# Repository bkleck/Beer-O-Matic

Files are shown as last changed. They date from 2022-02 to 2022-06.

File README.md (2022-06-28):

# Beer-O-Matic
Automatic Beer Dispenser



## Table of Contents
* [Introduction](#introduction)
* [Mechanical Design](#mechanical-design)
* [Code Documentation](#code-documentation)
* [Logic Diagram](#logic-diagram)
* [Wiring Diagram](#wiring-diagram)

## Introduction
This project was done as part of the **_ME102B Mechatronics Design_** course during my exchange in UC Berkeley. We had to produce a working prototype by the end of the semester, that solves a problem in real life. We had to do both **_mechanical design and code design_** for our prototype to work.

We decided to do something fun, and decided to build a **_automatic beer dispenser_**. This solves the problem which one might experience in a crowded bar, trying to get the attention of the bartender but to no avail. With our product, you will be able to get a cold pint of beer without the need to ask anybody!

## Mechanical Design


- A **_rack and pinion_** was designed so that the motor can move the dispensing spout along the rack to get to its **_target destination_**.
- A **_cup holder_** is placed at every seat so that the user can put their glass into the holder when they require a drink. A small **_push against the in-built button_** will signal to the system that the user **_requires a refill_**, without the need for manual effort.
- The 2 main sensors we used were the **_limit switches and the IR sensors_**. The limit switches will be placed on each end to signal to our system that it has reached the corners and to change direction, **_preventing our spout from falling off_** the rack. The IR sensors will be placed at each of the cup holders. This will help to track the moving spout, as well as to tell the system to **_stop when it has reached the target holder_**.

## Code Documentation
### 1) Position tracking
On `Startup()`, we will turn the motor anticlockwise to move left, and stop when it has reached the left limit. Afterwards, the direction will be reversed and `currentPos` will be set to 0, representing the left limit switch. There will be **_3 IR sensors_** in our demo, so each of them will be labelled 1,2,3 respectively and the right limit switch will be 4.

The `ReadTarget()` function will be used to **_add a target position_** to the queue. We will be using a **_FIFO queue system_** so that users can signal to the system that they require a drink at any point in time, without needing to wait for their turn. Whenever a user **_presses the button_** on the cup holder, the system will **_read the pin as LOW_** because we are using **_PULLUP mode_**. We will then **_check if the position is already in queue_** using the boolean variable `elementInside`. This prevents any user from hogging the system and prevent spillage in the event the user accidentally presses more than once. If `elementInside = false`, we will **_add that element into our_** `targetQueue` **_array_** at the next possible location.

The `ReadIRSensor()` function is used to **_determine if the moving spout passes by any of the IR sensors_**. It uses `analogRead` to determine the **_amount of light the IR sensor is receiving_** at that point in time. We will use the initial IR reading during startup to determine that as no object passing by. If the **_current reading drops 100 points below initial reading_**, this means the moving spout **_moved past_** and it will return a **_LOW value_**.

Our `MoveToTarget()` function does exactly what is said. The `targetPos` variable is the next position the spout needs to move to, which is the **_first element_** of the `targetQueue` array. Next, we will make use of the **_current position's index and target position's index to tell the spout where to move_**. If `targetIndex > currentIndex`, the spout needs to move right to reach the target, and vice versa. Once `targetPos == currentPos`, we have reached our destination and will **_dispense beer_** using `measure_dispense()` function. The element will also be **_removed from the queue_**. Another safety feature we had was that if the spout ever **_hits the left or right limit switches_**, we will **_reverse the direction_** so that it can continue to find the target position. This happens sometimes due to bugs in the IR sensors.

### 2) Dispensing
Firstly, to **_calculate the distance between the cup and pump_**, we have an **_ultrasound sensor_** attached to the spout. In the `calc_distance()` function, we will turn the trigger pin of this sensor from LOW to HIGH to LOW, and calculate the **_duration for the ultrasound wave to emit and reflect back_** from the bottom of the cup. The distance is then calculated by deriving from the **_duration recorded and the speed of sound in air_**.

Next, we will use the `measure_dispense()` function to actually dispense the beer in the given time. Firstly, we model our cup using a standard size of **_500ml_**, and we want the cup to be completely filled in **_~3s_**. Hence, we calculate the **_flow rate using volume/time_**. Afterwards, we calculate the rate of height increase required using **_height_rate = flow rate/surface area_**. Lastly, the **_time required for the dispense will be (distance - final_distance)/height_rate_**. We will then activate the relay pin to turn on the valve for the given amount of time. Another safety feature here is that when the valve is open, the motor will be turned off, and vice versa, to **_prevent any spillage_** from movement during dispensing.

## Logic Diagram
<p align="center">
  
  
  
</p>

## Wiring Diagram
<p align="center">
  
</p>

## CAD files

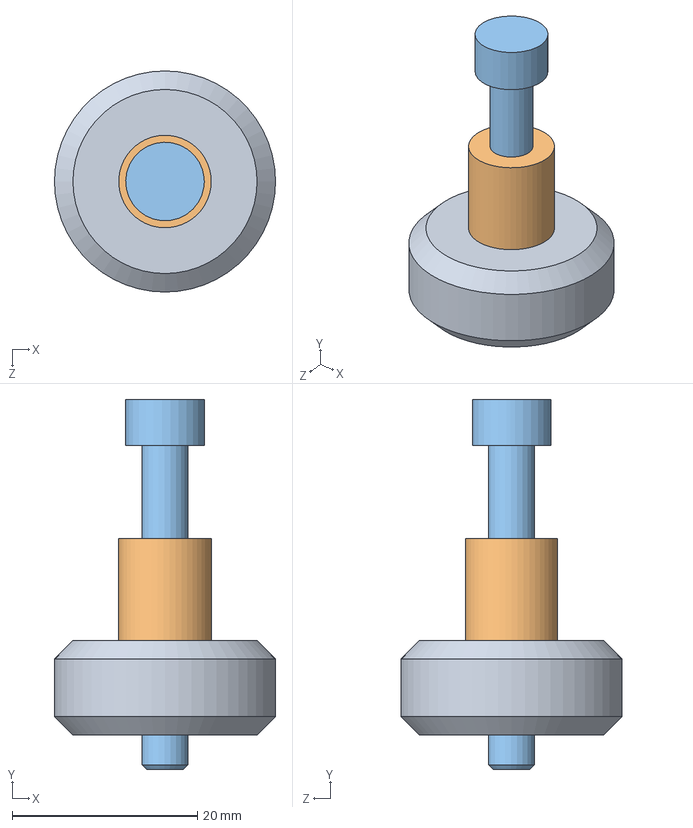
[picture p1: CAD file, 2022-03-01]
CAD files/PissBotV1 17-02-2022/PissBotV1 17-02/VWheelAssy.SLDASM
23.9 x 40.0 x 23.9 mm
Solid V Wheel
M5x9 Spacer
M5x40

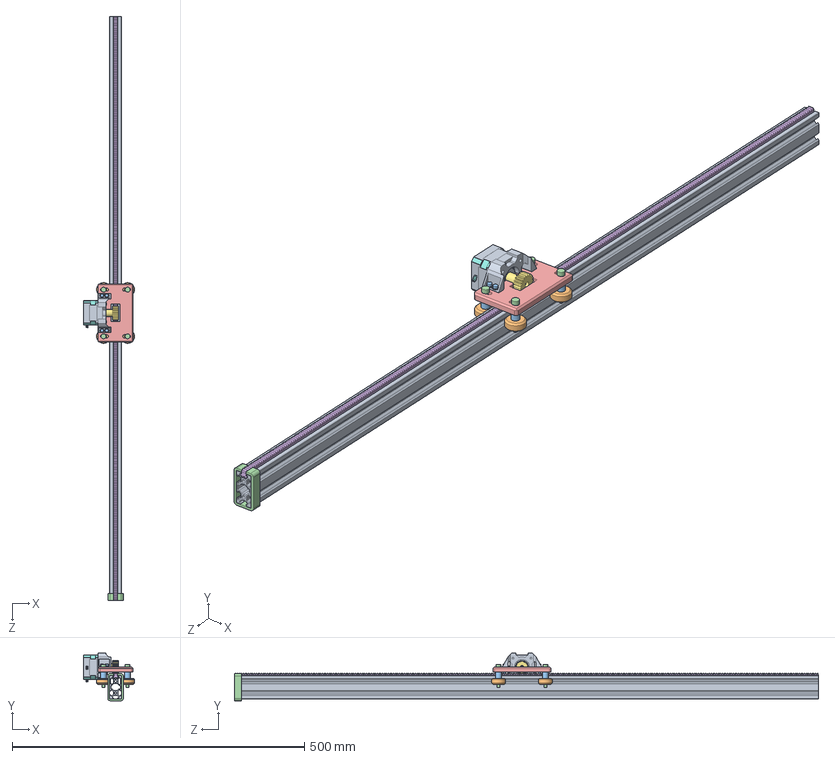
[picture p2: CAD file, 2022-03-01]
CAD files/All_Files_V1/PissBotV1.SLDASM
87.6 x 81.4 x 1000.0 mm
2040 V-Slot 500mm
Solid V Wheel x 4
M5x9 Spacer x 4
M5x40 x 4
Plate
Combined Rack Gear
Pinion Gear
Stepper Holder
M3 Washer x 8
M3x15 x 4
Rail Holder

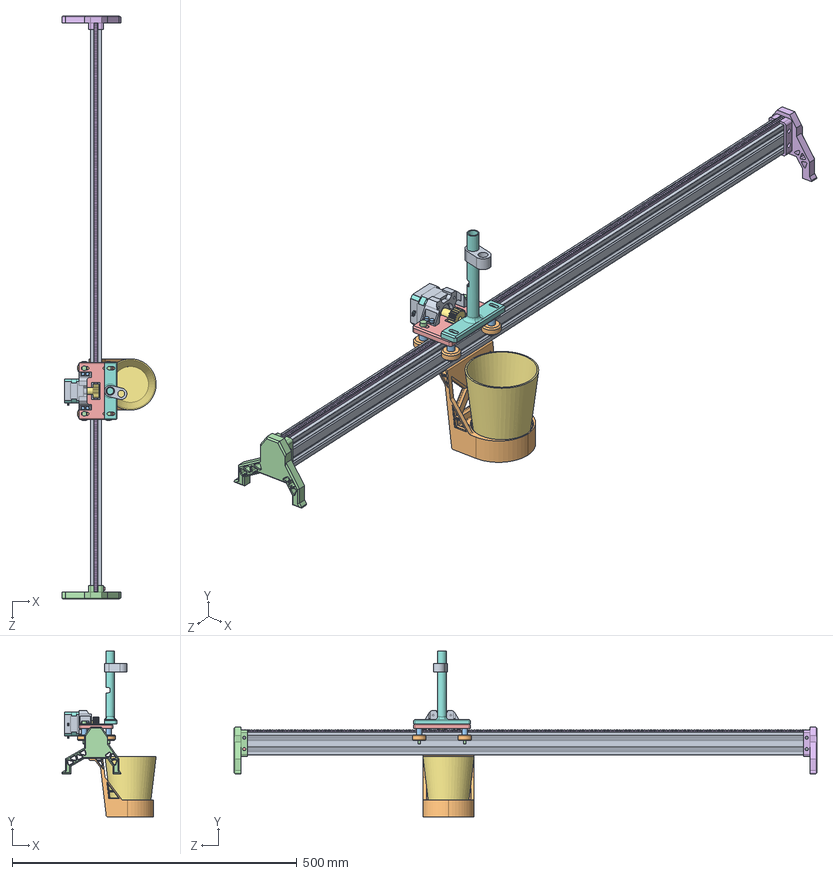
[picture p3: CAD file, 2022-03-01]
CAD files/PissBotV1 17-02-2022/PissBotV1 17-02/PissBotV1.SLDASM
165.7 x 291.1 x 1024.0 mm
2040 V-Slot 500mm
Solid V Wheel x 4
M5x9 Spacer x 4
M5x40 x 4
Plate
Combined Rack Gear
Pinion Gear
Stepper Holder
M3 Washer x 8
M3x15 x 4
Rail Holder
M4x8
Rail Holder Mirror
Cup
sprout_attachment
sprout_tip
Coaster V2

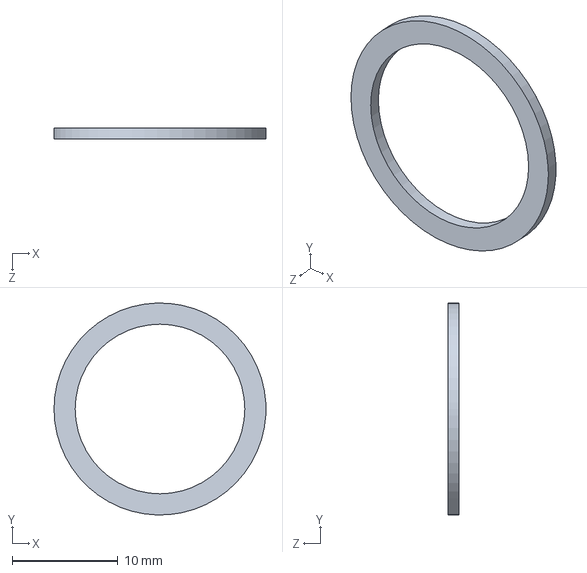
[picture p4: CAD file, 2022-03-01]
CAD files/All_Files_V1/Coaster Spacers.SLDPRT
20.0 x 20.0 x 1.00 mm

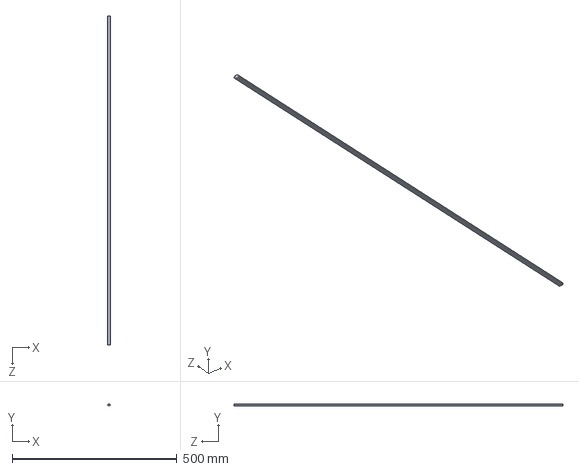
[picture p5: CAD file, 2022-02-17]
CAD files/Rack.SLDPRT
10.5 x 6.95 x 1000.0 mm

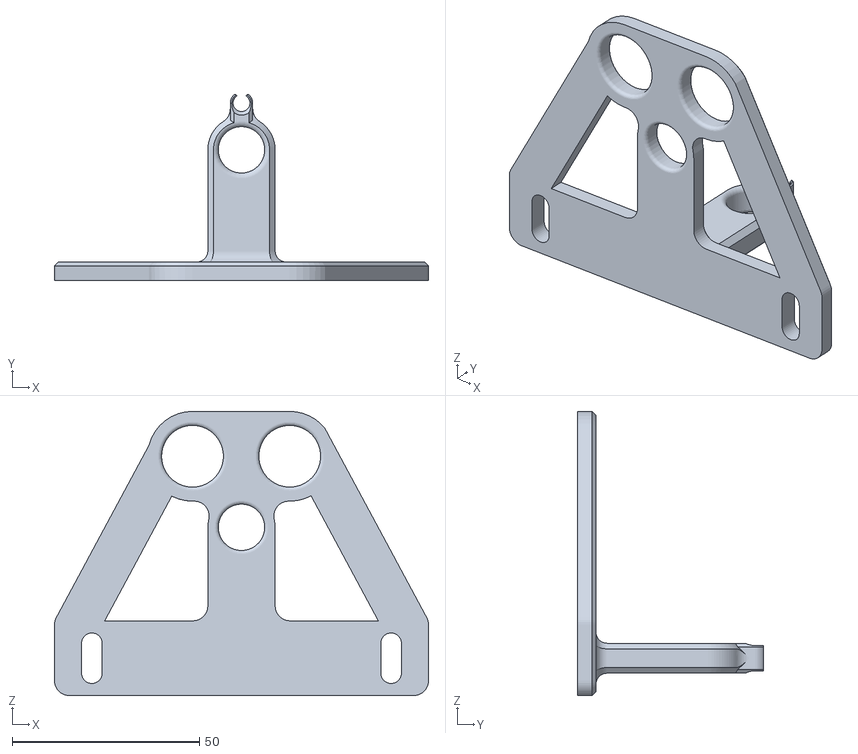
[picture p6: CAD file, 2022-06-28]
final CAD files/Spout V3.STL
100.0 x 49.9 x 76.0

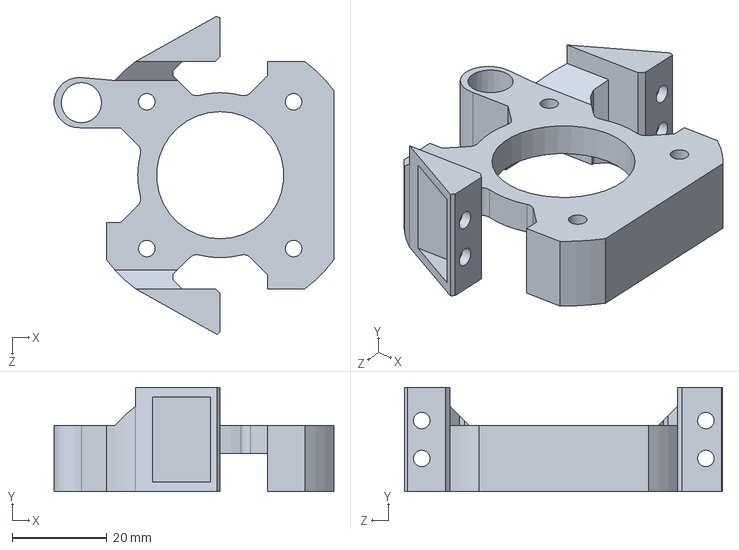
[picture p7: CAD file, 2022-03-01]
CAD files/All_Files_V1/Stepper Holder.sldprt
59.1 x 22.0 x 67.2 mm

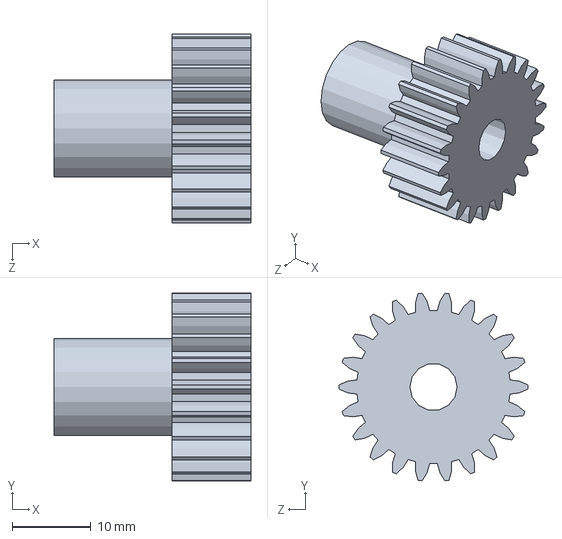
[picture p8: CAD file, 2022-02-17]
CAD files/Pinion Gear.SLDPRT
25.0 x 23.8 x 24.0 mm

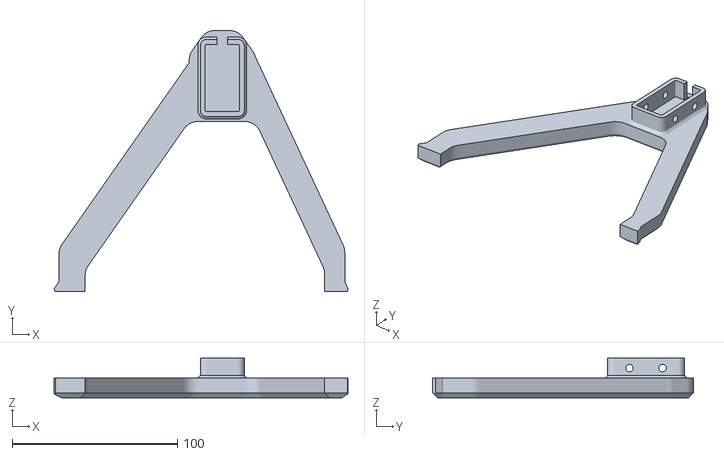
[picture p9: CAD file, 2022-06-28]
final CAD files/Rail Holder Mirror.STL
177.7 x 157.8 x 24.0

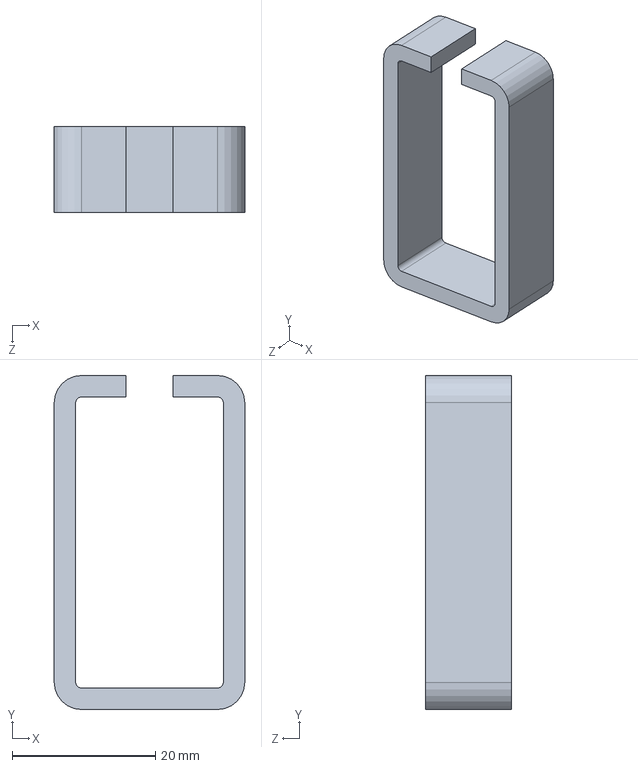
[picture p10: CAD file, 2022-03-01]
CAD files/All_Files_V1/Rail Holder.SLDPRT
26.6 x 46.6 x 12.0 mm

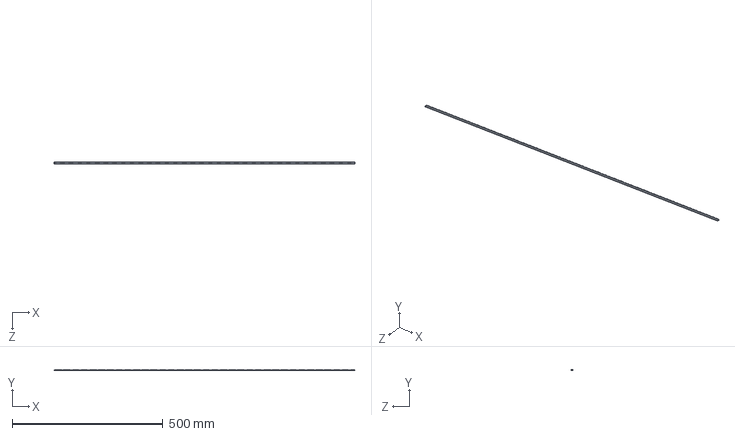
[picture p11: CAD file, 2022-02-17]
CAD files/Rack Gear.SLDPRT
1000.0 x 3.25 x 6.10 mm

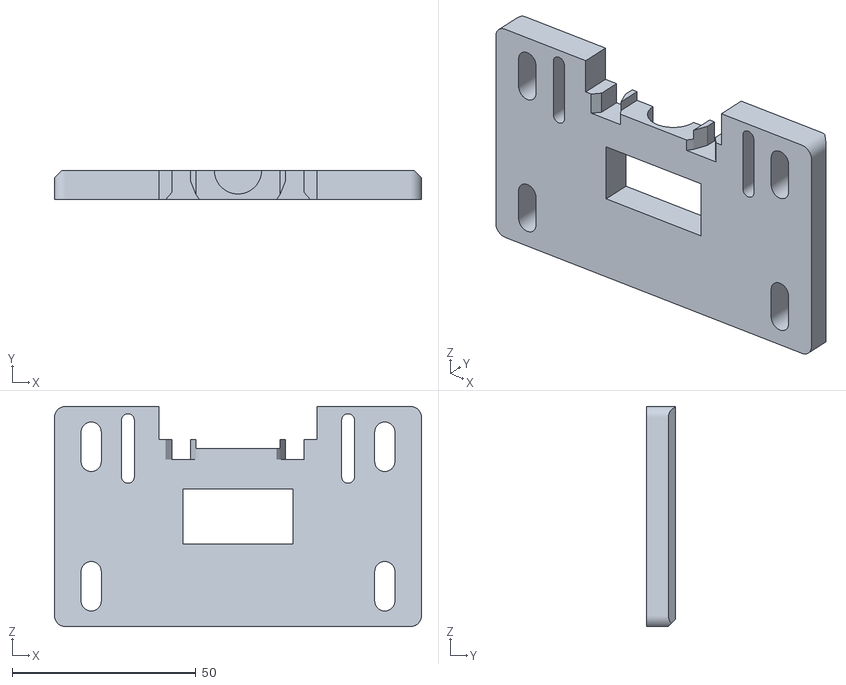
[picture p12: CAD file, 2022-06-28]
final CAD files/Plate.STL
100.0 x 8.00 x 60.0

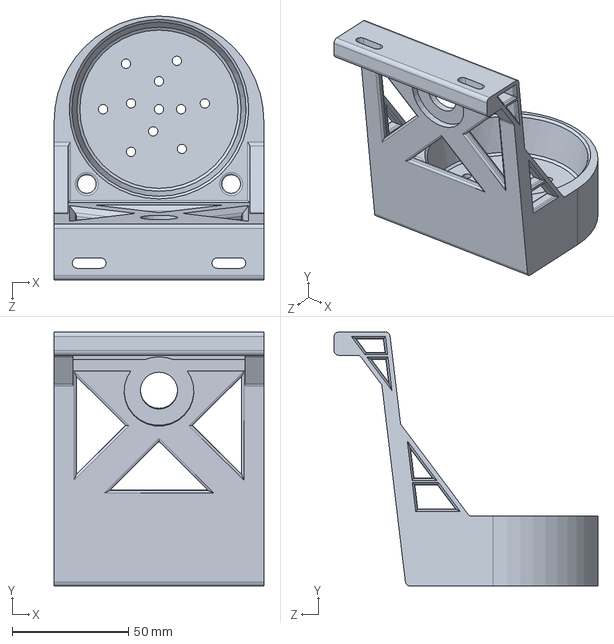
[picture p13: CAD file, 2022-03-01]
CAD files/All_Files_V1/Coaster V2.SLDPRT
90.0 x 109.0 x 113.3 mm

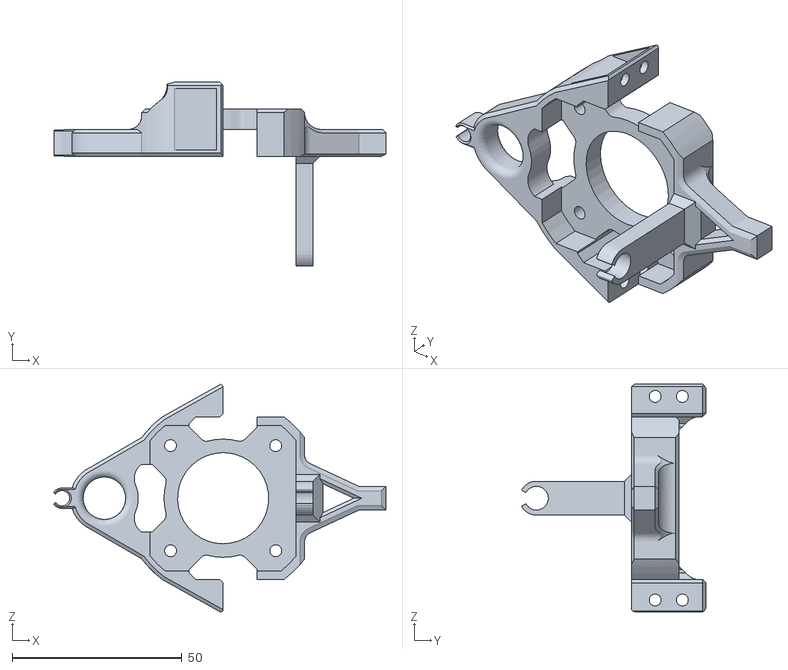
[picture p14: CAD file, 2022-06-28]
final CAD files/Stepper Holder.STL
97.9 x 54.3 x 67.2

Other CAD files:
CAD files/PissBotV1 17-02-2022/PissBotV1 17-02/VWheelAssy2.SLDASM
CAD files/PissBotV1 17-02-2022/PissBotV1 17-02/VWheelAssy4.SLDASM
CAD files/PissBotV1 17-02-2022/PissBotV1 17-02/VWheelAssy3.SLDASM
CAD files/All_Files_V1/Coaster.SLDPRT
CAD files/All_Files_V1/Cup.SLDPRT
CAD files/PissBotV1 17-02-2022/PissBotV1 17-02/2040 V-Slot 500mm.SLDPRT
CAD files/PissBotV1 17-02-2022/PissBotV1 17-02/9238.sldprt
CAD files/PissBotV1 17-02-2022/PissBotV1 17-02/Coaster.SLDPRT
CAD files/PissBotV1 17-02-2022/PissBotV1 17-02/Combined Rack Gear.SLDPRT
CAD files/PissBotV1 17-02-2022/PissBotV1 17-02/M3 Washer.SLDPRT
CAD files/PissBotV1 17-02-2022/PissBotV1 17-02/M3x15.SLDPRT
CAD files/PissBotV1 17-02-2022/PissBotV1 17-02/M4x8.SLDPRT
CAD files/PissBotV1 17-02-2022/PissBotV1 17-02/M5x40.SLDPRT
CAD files/PissBotV1 17-02-2022/PissBotV1 17-02/M5x9 Spacer.SLDPRT
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

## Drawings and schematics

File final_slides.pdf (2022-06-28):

# BEER - 0 -

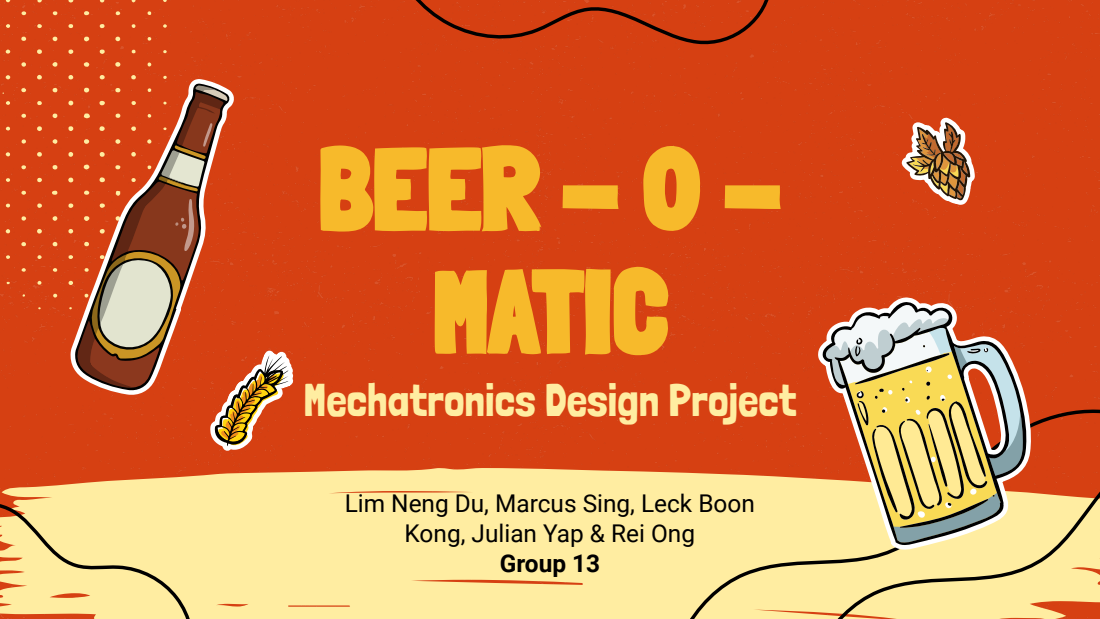
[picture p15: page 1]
MATIC; Group 13

Mechatronics Design Project

Lim Neng Du, Marcus Sing, Leck Boon
Kong, Julian Yap & Rei Ong

# Problem

# Solution

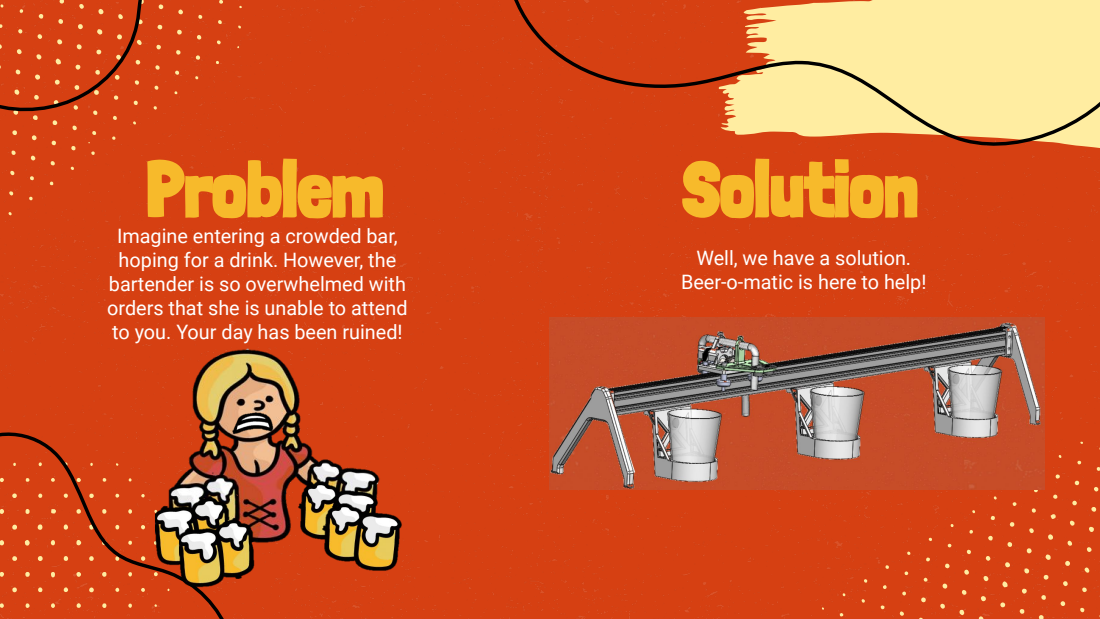
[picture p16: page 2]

Imagine entering a crowded bar,
hoping for a drink. However, the
bartender is so overwhelmed with
orders that she is unable to attend
to you. Your day has been ruined!

Well, we have a solution.
Beer-o-matic is here to help!

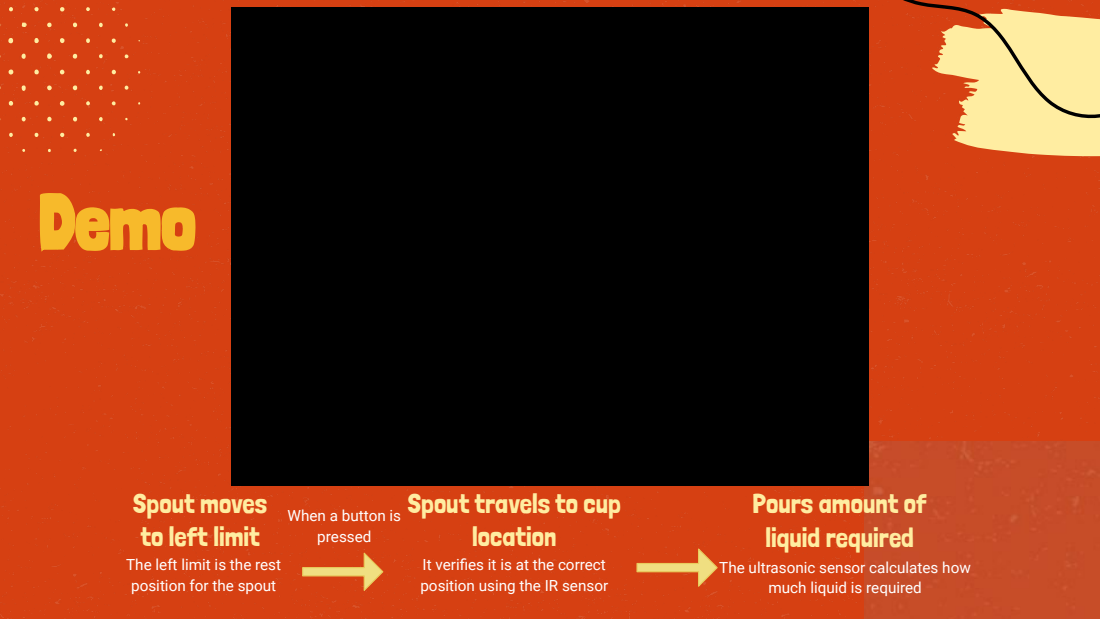
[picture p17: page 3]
Demo

Spout moves
to left limit

Spout travels to cup
location

Pours amount of
liquid required

When a button is
pressed

The left limit is the rest
position for the spout

It verifies it is at the correct
position using the IR sensor

The ultrasonic sensor calculates how

much liquid is required

# Logic Diagram

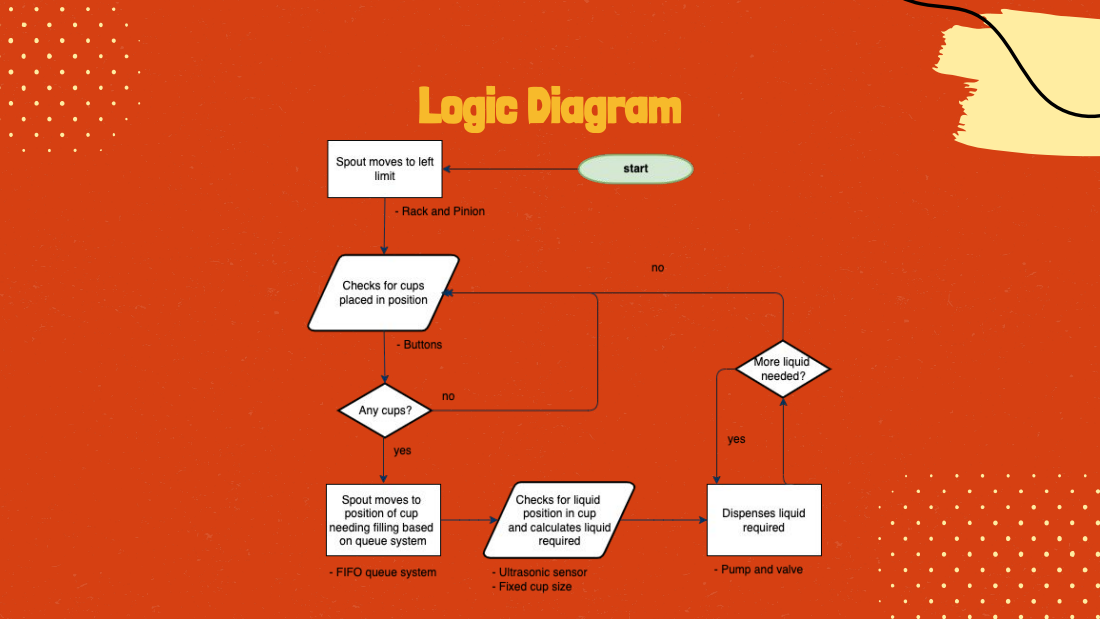
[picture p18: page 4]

# Logic Diagram

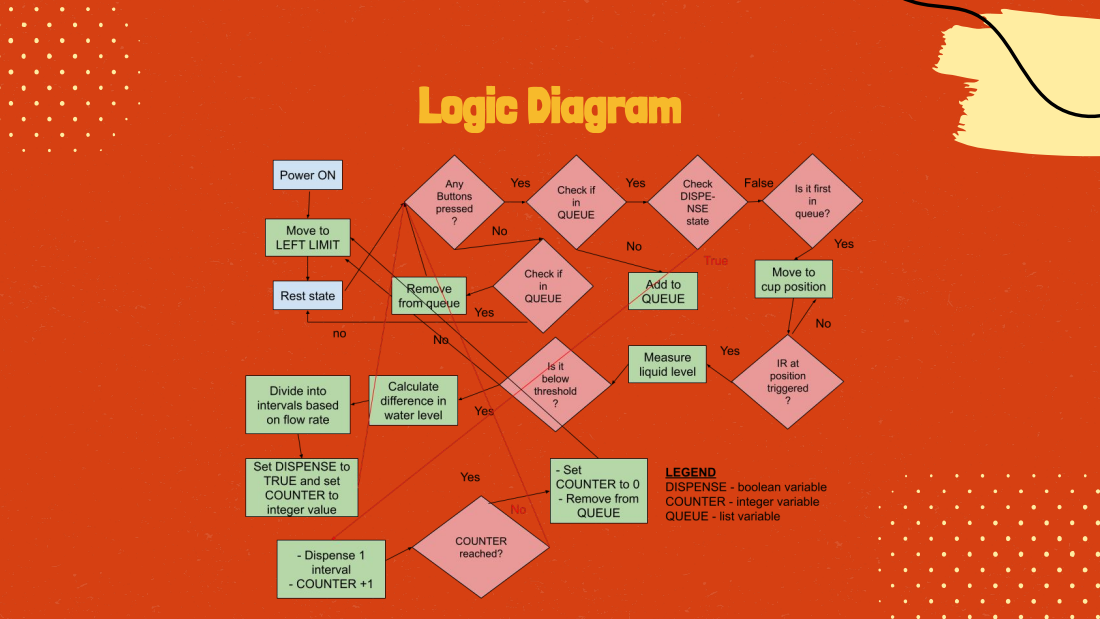
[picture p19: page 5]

# Physical characteristics

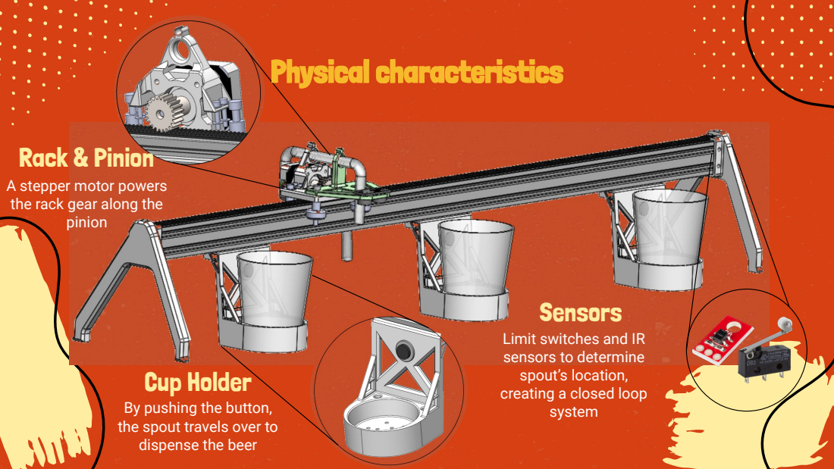
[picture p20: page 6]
Cup Holder; pinion; Sensors; system; Rack & Pinion

A stepper motor powers
the rack gear along the

Limit switches and IR
sensors to determine
spout’s location,
creating a closed loop

By pushing the button,
the spout travels over to
dispense the beer

# Program logic

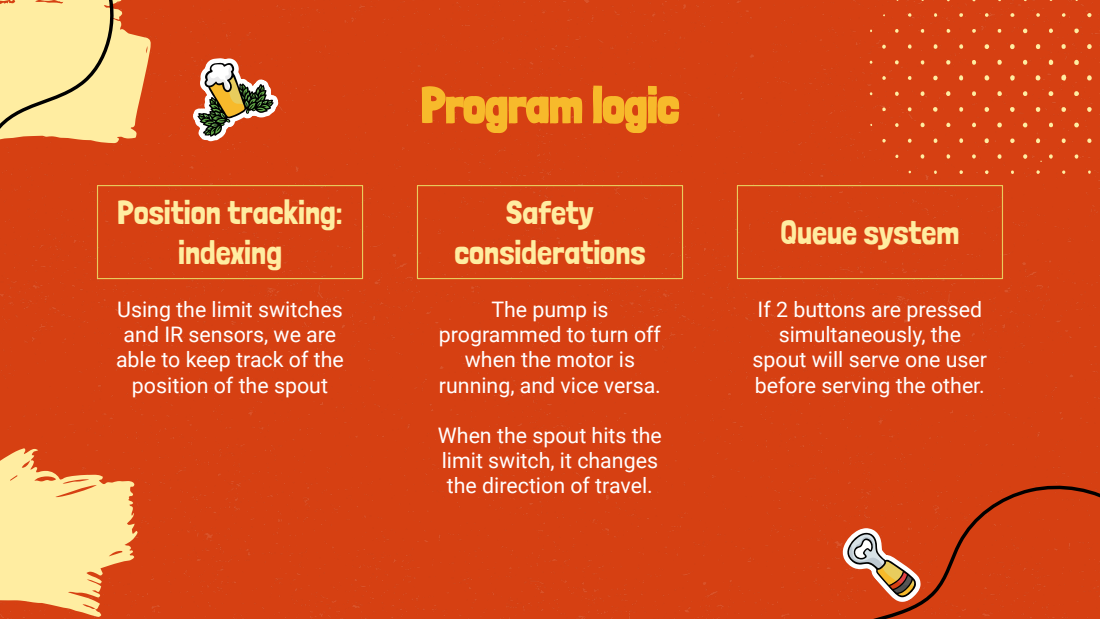
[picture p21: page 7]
Position tracking: indexing; Safety considerations; Queue system

Using the limit switches
and IR sensors, we are
able to keep track of the
position of the spout

The pump is
programmed to turn off
when the motor is
running, and vice versa.

If 2 buttons are pressed
simultaneously, the
spout will serve one user
before serving the other.

When the spout hits the
limit switch, it changes
the direction of travel.

# Engineering principles

# Pump System

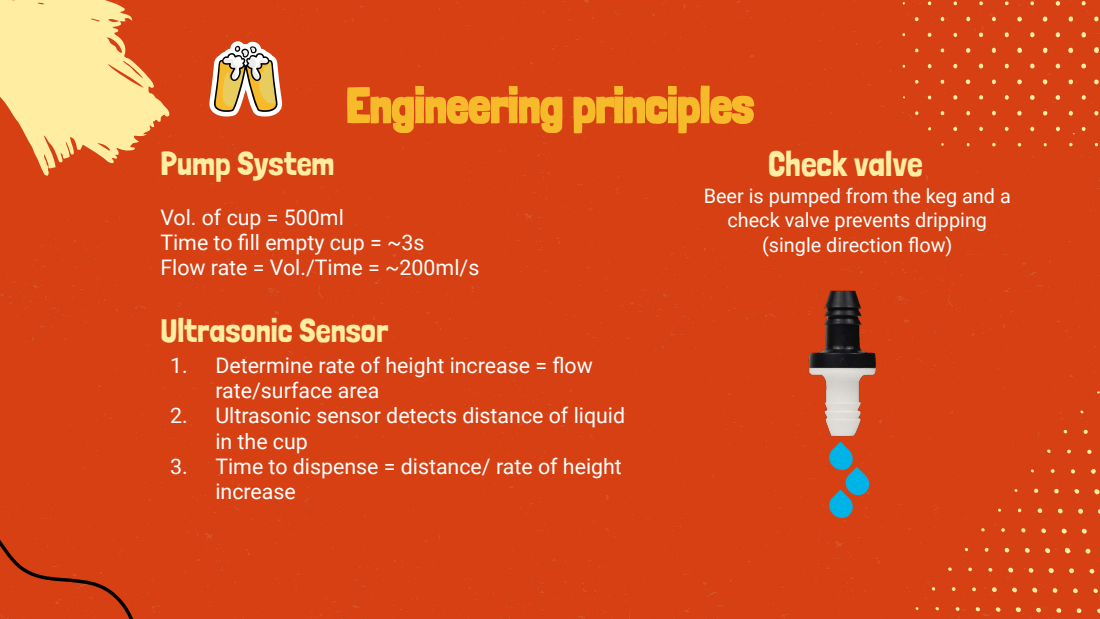
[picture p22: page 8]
Check valve

Beer is pumped from the keg and a
check valve prevents dripping
(single direction flow)

Vol. of cup = 500ml
Time to fill empty cup = ~3s
Flow rate = Vol./Time = ~200ml/s
Ultrasonic Sensor

1. Determine rate of height increase = flow
rate/surface area
2. Ultrasonic sensor detects distance of liquid
in the cup
3. Time to dispense = distance/ rate of height
increase

# Fluid Pump

# Linear Movement Spout

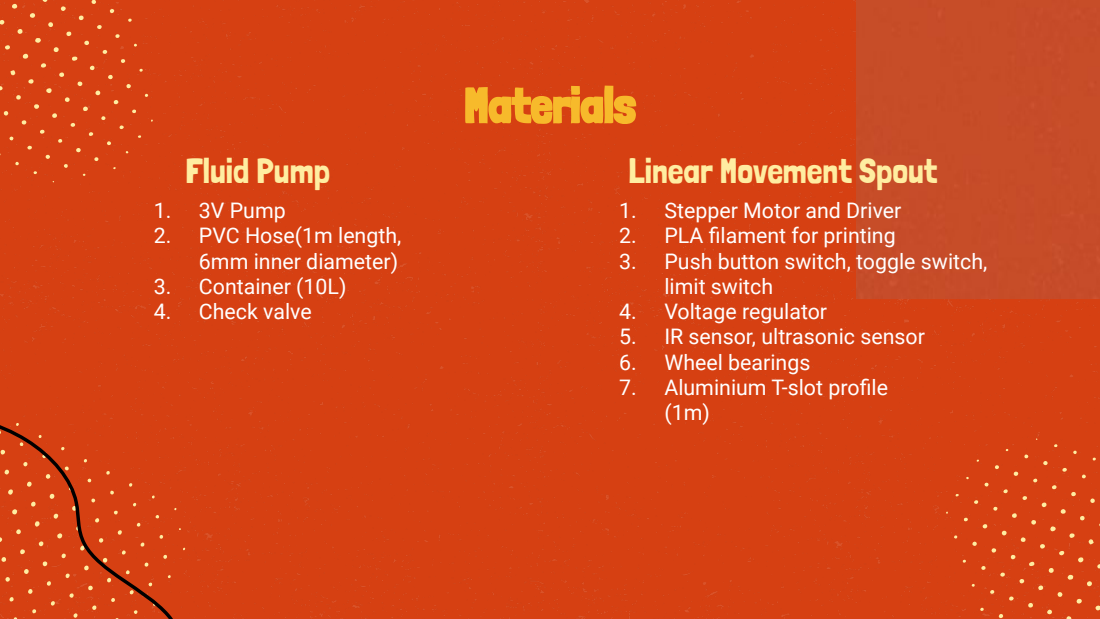
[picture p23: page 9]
Materials

1. 3V Pump
2. PVC Hose(1m length,
6mm inner diameter)
3. Container (10L)
4. Check valve

1. Stepper Motor and Driver
2. PLA filament for printing
3. Push button switch, toggle switch,
limit switch
4. Voltage regulator
5. IR sensor, ultrasonic sensor
6. Wheel bearings
7. Aluminium T-slot profile

# Future work

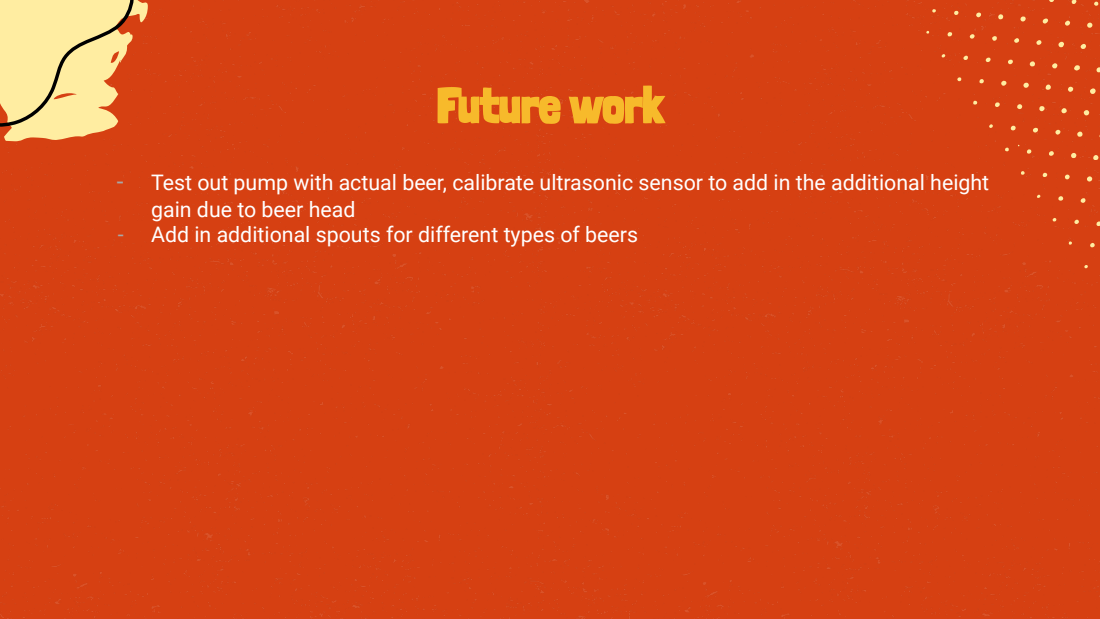
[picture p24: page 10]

- Test out pump with actual beer, calibrate ultrasonic sensor to add in the additional height
gain due to beer head
- Add in additional spouts for different types of beers

# Thanks!

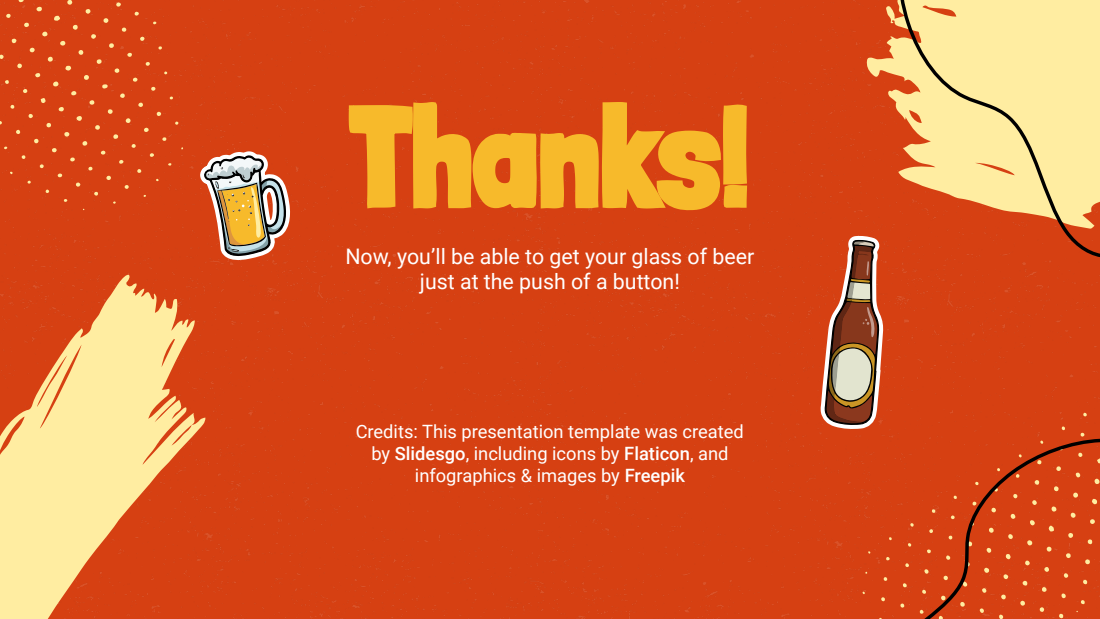
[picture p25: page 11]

Now, you’ll be able to get your glass of beer

just at the push of a button!

Credits: This presentation template was created
by Slidesgo, (http://bit.ly/2Tynxth) including icons by Flaticon, (https://flaticon.com/) and
infographics & images by Freepik (https://freepik.com/)

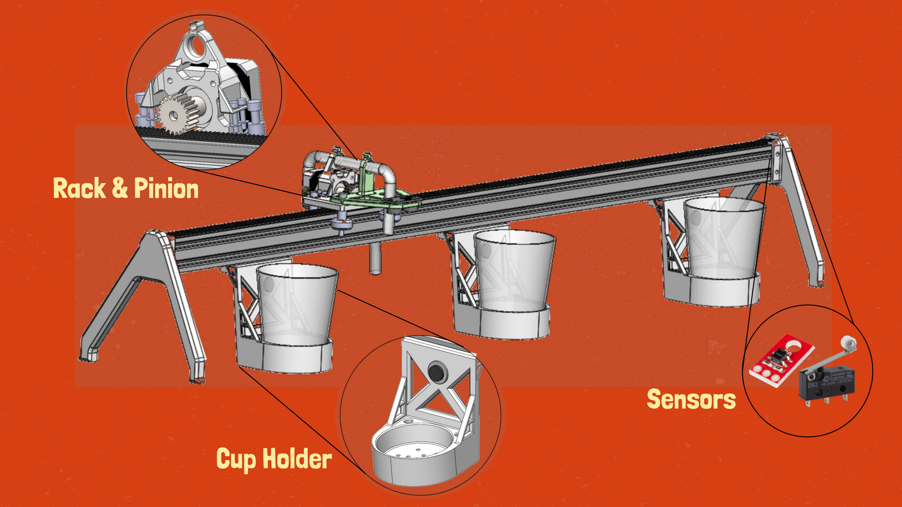
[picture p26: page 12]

# Rack & Pinion

# Cup Holder

# Sensors

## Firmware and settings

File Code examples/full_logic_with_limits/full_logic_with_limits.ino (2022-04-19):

#include "SparkFun_ProDriver_TC78H670FTG_Arduino_Library.h"
#include <ezButton.h>

PRODRIVER myProDriver; //Create instance of driver

// for main mechanism
const int leftLimit = 12;
const int rightLimit = 11;
const int IR1 = A0;
const int IR2 = A3;
const int IR3 = A5;
const int Button1 = 50;
const int Button2 = 51;
const int Button3 = 52;

// for pump
#define trigPin 27
#define echoPin 33
#define relayPin 22
float duration, distance, time_required;
float final_distance = 5; // 5(ultra to cup top) + 2 (buffer)
float flow_rate = 22.2; //cm^3 per second (to be determined)
float surface_area = 43; // (to be determined)
float height_rate = flow_rate/surface_area; //rate of height increase
int count = 0; //counter for millis
float max_time = 20; //maximum pump run time
//int buffer_time = 2;// time require for water to reach tip of tube from tank(seconds)
long previousMillis = 0;


bool limit;

int dir = 0;
int init_light_reading;

int currentPos;
const int sequence[5] = {0, 1, 2, 3, 4};
int targetQueue[3] = {0, 0, 0};
int currentIndex;
int targetIndex;

/* function to call when the circuit is first turned on
 *  this will turn the motor anticlockwise towards the left limit
 *  stops when it hits the left limit
 */
void Startup() {
  while (ReadPin(leftLimit)) {
    myProDriver.step(1, dir);
  }

  Serial.println("reached left limit");
  currentPos = 0;
  dir = dir + 1;
  delay(3000);
}


// function to read digital pins, returning 1 or 0
bool ReadPin(int pinNumber) {
  bool result = digitalRead(pinNumber);
  return result;
}



// function to set the target position to the queue whenever a button is read LOW due to PULLUP mode
char ReadTarget() {

  int queueSize = 0;
  // reset queueSize based on position of first zero
  // this queueSize will be used as the index to add the latest element to the list
  for (int i = 0; i < 5; i++) {
    if (targetQueue[i] == 0) {
      queueSize = i;
      break;
    }
  }
  // Serial.println((String) "queue size:" + queueSize);
  
  if (ReadPin(Button1) == LOW) {
    Serial.println("button 1 pressed");
    bool elementInside1 = false;
    // if any element inside the queue is I, this means that the element is already inside
    for (int i = 0; i < 4; i++) {
      if (targetQueue[i] == 1) {
        elementInside1 = true;
      }
    }
    // only add the element to the queue if it was not inside already
    if (elementInside1 == false) {
      targetQueue[queueSize++] = 1;
    }
}

  if (ReadPin(Button2) == LOW) {
    Serial.println("button 2 pressed");
    bool elementInside2 = false;
    for (int i = 0; i < 4; i++) {
      if (targetQueue[i] == 2) {
        elementInside2 = true;
      }
    }
    if (elementInside2 == false) {
      targetQueue[queueSize++] = 2;
    }
}

  if (ReadPin(Button3) == LOW) {
  Serial.println("button 3 pressed");
    bool elementInside3 = false;
    for (int i = 0; i < 4; i++) {
      if (targetQueue[i] == 3) {
        elementInside3 = true;
      }
    }
    if (elementInside3 == false) {
      targetQueue[queueSize++] = 3;
    }
}
}


// function to set the current position whenever a limit switch or IR sensor is activated
// as the pins are on PULLUP mode, they are activated when read as LOW
char ReadCurrent() {
  if (ReadPin(leftLimit) == LOW) {
    currentPos = 0;
  }
  
  else if (ReadPin(rightLimit) == LOW) {
    currentPos = 4;
  }

  else if (ReadIRSensor(IR1) == LOW) {
    currentPos = 1;
  }

  else if (ReadIRSensor(IR2) == LOW) {
    currentPos = 2;
  }
  
  else if (ReadIRSensor(IR3) == LOW) {
    currentPos = 3;
  }
}


/* Function to read the IR sensors
 * IR sensors are connected to analog pins giving raw integer values
 * I defined HIGH as the initial reading of IR1 at startup
 * and the current reading as LOW when current reading goes below 100 of initial reading
 */
bool ReadIRSensor(int IR_pin) {
  int light_reading = analogRead(IR_pin);
  if (light_reading <= init_light_reading - 100) {
    Serial.println("Something fat passed by: " + IR_pin);
    return 0;
  }
  else {
    return 1;
  }
}


/*
 * function to move to target position 
 * get the index of the target and current position within the sequence array
 * if the target index is greater, means it should move to the right
 * if the target index is smaller, means it should move left
 * 
 * if the target position is equal to current position, the motor will not move
 * if not it will move based on the direction given above
 */
void MoveToTarget() {
  int targetPos = targetQueue[0];
  Serial.println((String) "Target position: " + targetPos);
  if ((targetPos != NULL) & (targetPos != 0)) {
    for (int i=0; i < 5; i++) {
      if (targetPos == sequence[i]) {
        targetIndex = i;
      }
      else if (currentPos == sequence[i]) {
        currentIndex = i;
      }
    }

    if (targetIndex > currentIndex) {
      dir = 1;
    }

    else if (targetIndex < currentIndex) {
      dir = 0;
    }

    if (targetPos == currentPos) {
      // once reach the position, dispense liquid
      measure_dispense();
      
      // once reached, remove the first element from the array
      for (int i=1; i<3; i++) {
        targetQueue[i-1] = targetQueue[i];
      }
    }

    // reverses the directions if it hits the left or right limit
    // if its at the left limit, it should move right
    else if (currentPos == 0) {
      dir = 1;
      myProDriver.step(3, dir);
    }

    // if its at the right limit, it should move left
    else if (currentPos == 4) {
      dir = 0;
      myProDriver.step(3, dir);
    }

    else {
      myProDriver.step(3, dir);
    }
  }
}


/* function to calculate distance between cup and pump
 *  this is done by calculating the time for ultrasound wave to reflect
 *  and divide it by the speed of sound
 */
void calc_distance (){
  digitalWrite(trigPin, LOW);
  delayMicroseconds(2);
  digitalWrite(trigPin, HIGH);
  delayMicroseconds(10);
  digitalWrite(trigPin, LOW);

  duration = pulseIn(echoPin, HIGH);
  distance = (duration*.0343)/2;
  Serial.println(distance);
}

/* function to dispense liquid from the pump after distance has been calculated
 * make use of count to ensure it only dispenses once
 */
void measure_dispense() {
  calc_distance();
  Serial.println(distance);
  time_required = (distance-final_distance)/height_rate;
  if (time_required > max_time){
    time_required = max_time;
  }
  Serial.println(time_required);

  long currentMillis = millis();
  count = 0;
  previousMillis = currentMillis;
  while (currentMillis - previousMillis < time_required*1000) {
    
    if (count == 0){
      myProDriver.disable();
      digitalWrite(relayPin,HIGH);
      previousMillis = currentMillis;
      count = 1;
    }
    myProDriver.disable();
    digitalWrite(relayPin,HIGH);
    currentMillis = millis();
    // ReadTarget();
    }

  digitalWrite(relayPin,LOW);
  myProDriver.enable();

}


void setup() {
  Serial.begin(115200);
  pinMode(12, INPUT_PULLUP);
  pinMode(11, INPUT_PULLUP);
  
  pinMode(50, INPUT_PULLUP);
  pinMode(51, INPUT_PULLUP);
  pinMode(52, INPUT_PULLUP);
  
  pinMode(trigPin, OUTPUT);
  pinMode(echoPin, INPUT);
  pinMode(relayPin, OUTPUT);
  myProDriver.begin();
  // get initial reading for comparison when motor moves past
  init_light_reading = analogRead(IR1);
  Startup();
}

void loop() {
  Serial.println("Target Queue Elements:");
  for (int i=0; i<3; i++) {
    Serial.println(targetQueue[i]);
  }

  ReadTarget();
  ReadCurrent();
  Serial.println((String)"current position: " + currentPos); 
  MoveToTarget();
}

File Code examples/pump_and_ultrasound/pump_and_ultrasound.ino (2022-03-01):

#define trigPin 32
#define echoPin 14
#define relayPin 25
float duration, distance, time_required;
int offset_distance = 2; // distance from tube tip to cup tip (cm)
int edge_distance = 10; //distance from top of the cup to final height (cm)
int flow_rate = 5; //litres per second (to be determined)
int surface_area; // (to be determined)
int height_rate = flow_rate/surface_area; //rate of height increase
int buffer_time = 2;// time require for water to reach tip of tube from tank(seconds)
long previousMillis = 0;


void setup() {
  // put your setup code here, to run once:
  pinMode(trigPin, OUTPUT);
  pinMode(echoPin, INPUT);
  pinMode(relayPin, OUTPUT);

}

void loop() {
  calc_distance();
  time_required = (distance-offset_distance-edge_distance)/height_rate;
  unsigned long currentMillis = millis();
  // Keeps the pump running until fill time is reached
  while(currentMillis - previousMillis < time_required+ buffer_time){
    digitalWrite(relayPin,HIGH);// relayPin controls whether pump is ON/OFF
    previousMillis = currentMillis;}
    
  digitalWrite(relayPin,LOW);
}

//distance from ultrasound sensor to level of water in the cup
void calc_distance (){
  digitalWrite(trigPin, LOW);
  delayMicroseconds(2);
  digitalWrite(trigPin, HIGH);
  delayMicroseconds(10);
  digitalWrite(trigPin, LOW);

  duration = pulseIn(echoPin, HIGH);
  distance = (duration*.0343)/2;
}

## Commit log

2022-02-16 created rack
    [Rack.SLDPRT]
2022-02-17 Pinion and Rack Gears v1
    [Pinion Gear.SLDPRT, Rack Gear.SLDPRT]
2022-02-17 bottom of rack
    [Rack.SLDPRT]
2022-02-17 detect water level with HC-SR04
    [Rack.SLDPRT]
2022-02-17 fixed sensor drift
    add 10k resistor to TRIGGER pin
    [ultrasonic_test.ino]
2022-02-17 All CAD files related to Rack and Pinion System, with Stepper Motor, Motor holder, Horizontal plate etc
    [2040 V-Slot 500mm.SLDPRT, 9238.sldprt, Combined Rack Gear.SLDPRT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]
2022-02-17 updated plate and stepper holder
    [Plate.SLDPRT, Stepper Holder.sldprt]
2022-02-17 Changed Assembly File
    [PissBotV1.SLDASM]
2022-02-17 Added date-time text
    [PissBotV1.SLDASM]
2022-02-17 Update Stepper Holder.sldprt
    [Stepper Holder.sldprt]
2022-02-17 sprout files
    sprout attachment and sprout tip
    [sprout_attachment.SLDPRT, sprout_tip.SLDPRT]
2022-02-18 coaster (not done)
    [Coaster.SLDPRT]
2022-02-18 5pm Commit
    [PissBotV1.SLDASM, Rail Holder.SLDPRT]
2022-02-23 cup CAD + updated coaster
    [Coaster.SLDPRT, Cup.SLDPRT]
2022-02-23 new coaster design
    [Coaster V2.SLDPRT, Coaster.SLDPRT]
2022-02-23 updated assembly with sprout n coaster
    [2040 V-Slot 500mm.SLDPRT, 9238.sldprt, Coaster.SLDPRT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]
2022-02-23 slanted coaster
    [Coaster V2.SLDPRT, PissBotV1.SLDASM]
2022-02-28 weird updates
    [PissBotV1.SLDASM, VWheelAssy.SLDASM, VWheelAssy2.SLDASM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]
2022-02-28 button extrusion on coaster
    [Coaster V2.SLDPRT, PissBotV1.SLDASM]
2022-02-28 small update
    [Coaster V2.SLDPRT, PissBotV1.SLDASM]
2022-02-28 coaster + spacers
    [Coaster Spacers.SLDPRT, Coaster V2.SLDPRT, PissBotV1.SLDASM]
2022-03-01 Create pump_and_ultrasound.ino
    for the ultrasonic sensor and pump code
2022-03-14 motor moves to target (1 button)
2022-03-14 works with moving to 2 buttons
2022-04-06 added 3rd button and IR
2022-04-11 integrated pump code
2022-04-11 test with pump
2022-06-28 printed CAD files
    [IR Sensor Holder.STL, Plate.STL, Rail Holder Mirror.STL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]
